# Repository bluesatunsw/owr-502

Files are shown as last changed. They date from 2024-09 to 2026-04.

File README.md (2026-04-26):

# owr
This repo includes all software necessary to operate the Test Rover Platform
that is being designed and developed in the OWR project.

## System Setup
A guide is available on the
[owr-docs](https://github.com/bluesatunsw/owr-docs/tree/main/src/guides/container_setup.md)
repository.

## Useful Command index
| Command | Effect |
| --- | --- |
| `podman compose -f "$PWD/.devcontainer/docker-compose.yml" up -d` | Run in the git root to build/restart/start the Docker container. |
| `podman compose -f "$PWD/.devcontainer/docker-compose-obc.yml" up -d` | Run in the git root to build/restart/start the Docker container **with obc specific settings!** |
| `podman exec -it --latest /bin/bash` | Enter the docker container after launching it with the devcontainer. |
| `./utils/init.bash` | Run after `cd`'ing into `/workspaces/owr` in the container to source the ROS env and tools |
| `colcon build --symlink-install` | Runs the `colcon` meta build system, builds ALL rover packages! |
| `ros2 launch rover rover.launch.py` | Launch the robot state publisher. Just leave this running. |
| `rqt` | The flexible ROS2 viewer, useful for debugging topic flows and looking at raw topics. |
| `rviz2` | Useful for visualizing TF2 / LiDAR / etc... data to see if it looks okay. |
| `podman rm --force --latest -t 0` | Kill the podman container with the latest creation date (quickly) |

NOTE: `podman compose` will take a VERY long time! on uni Wi-Fi \~5min due to
the amount of packages it installs (\~5GB). There is also [a podman
bug](github.com/containers/podman/issues/16541) that invokes a postprocessing
step on the overlay filesystem, this will take **upwards of 10 minutes!** 

NOTE: `./utils/init.bash` will source the appropriate files as well as put you
in a 10-deep nested shell - running an invalid command will kill 1 level!

### Less Common Commands

| Command | Effect |
| --- | --- |
| `ros2 launch rover rsp.launch.py` | Robot State Publisher, publishes the URDF+JSP, to make it viewable in Lichtblick / Rviz2. |
| `xacro ./src/rover/description/robot.urdf.xacro > ./build/rover.urdf` | Compiles the xacro into a singular urdf file |
| `ros2 run key_teleop key_teleop --ros-args -p twist_stamped_enabled:=True -r /key_vel:=/diff_drive_base_controller/cmd_vel` | Record keyboard imputs and publish them as Twist2d values, which ROS2Control is listening for! |

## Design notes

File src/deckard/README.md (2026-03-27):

# REPL for controlling the rover over Cyphal

Run the program:
`deckard <stepper can interface> <VESC can interface> <OBC node ID>`

e.g. `deckard can0 can1 43`

The program has integrated help.

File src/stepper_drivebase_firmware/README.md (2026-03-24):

# Stepper drivebase firmware

See also `main.rs` (and maybe `Cargo.toml`).

## Firmware organisation

This crate uses the `embedded_common` crate, which should be shipped and
checked out in this crate's parent directory (see `Cargo.toml`). This provides
STM32G4-specific drivers that are reused across Bluesat firmware for different
boards (e.g. Cyphal/canadensis FDCAN driver), and some other tools (e.g.
OpenOCD config files), which should be clear reading the following section.

Otherwise, we have a pretty normal-style flat module hierarchy.

## Running and debugging the firmware

To run the firmware in a debugging/development context with an ST-LINK connected:

```
openocd -f ../embedded_common/tools/stm32g4x.cfg
cargo run --release
```

It's pretty much necessary to run in release mode due to space optimisations
being necessary to fit onto the dozens of KB of device flash.

To flash the firmware *and have it continue to run after you disconnect the
debugger* (for integration testing, or the competition (!)), do *not* run
OpenOCD. Instead, with the debugger connected, run:

```
cargo flash --release --chip stm32g474rbtx
```

(You may need to install `cargo flash`.)

Ideally, we would add extra configuration to the different release profiles
(i.e. `debug` and `release`) so that `debug` actually fits into the flash *and*
provides a nonzero amount of helpful debug information, but we haven't gotten
around to doing this yet. (Keen beans, take note!)

## A note on DSDL

The `dsdl/` directory has been removed since we don't currently plan to use any
non-publically regulated types. If we ever do need them then just create the
directory again and add the types as in the `canadensis_mvp` crate (available
at all good Bluesat repositories near you).

## Message IDs for Cyphal

For the stepper motor, subject-IDs for drive commands are in the form `30xy`:

- `30` means the message is intended for the drivebase
- `x` is the channel identifier:
    - 0 to 3 refer to the front-left (FL), front-right (FR), back-left (BL) and
      back-right (BR) motors respectively (in the context of the drivebase).
      These also correspond to the CH0 to CH3 designations as printed on the
      board's silkscreen.
- `y` is the "topic", which currently has underspecified semantics. Just use `0`.

A message with subject-ID 3020, for example, is a drive command targeting the
back-left stepper motor.

## A historical note

This firmware formerly had provisions for being flashed to multiple different
chips across the STM32G4 and G0 families, with the target board being specified
as a build feature. This mechanism is demonstrated in `canadensis_mvp`. To
avoid stretching development effort too thinly, this has since been removed.
The current policy is that this firmware will always target and be maintained
solely for the latest revision of the board, which as of the time of writing
is:

Rev. 3p0

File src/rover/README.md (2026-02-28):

## Structure of description folder

`<xacro:include>`'s / xacro files in general are processed with a guaranteed evaluation order (top to bottom).

Thus all 'helper' files used across multiple subfiles have been included directly in the largest scope, `robot.urdf.xacro`

- robot.urdf.xacro
    - utils/inertial_macros.xacro
    - utils/materials.xacro
    - chassis/chassis.xacro
    - drivebase/drivebase.xacro
        - drivebase/db_helpers.xacro
        - ros2_control.xacro
    - utils/gazebo_plugins.xacro

## Important launch files
- `rsp.launch.py`
  - This will use the URDF to show a model of the rover and the full TF tree
  - Use rviz2 to view this, 
    - set `Fixed Frame` to `base_link`
    - Add a RobotModel, set `Description Topic` to `/robot_description`
    - (Optional) add a TF

- `simulation.launch.py`
  - This will launch a simulation of the **entire rover** (with a swerve drivebase)
  - It will launch a gazebosim window with the simulated 'moon' environment
  - You may use rviz2 to view joint states etc..

### You may also want to launch:

- `ros2 run key_teleop key_teleop --ros-args -p twist_stamped_enabled:=True -r /key_vel:=/swerve_drive_base_controller/cmd_vel`
    - Runs a small TUI application that listens to arrow keys, and publishes a twist based on this (used for driving around the robot)
    - You will need to install `ros-jazzy-key-teleop` (with apt) first

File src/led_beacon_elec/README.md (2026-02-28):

# LED Beacon

I've measured it to be around 155mm wide by 40mm tall

This is gonna cost around $29

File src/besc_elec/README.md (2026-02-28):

# NOTES FROM CREATOR

### Datasheets:
- DRV8301 Gate Driver https://www.ti.com/lit/ds/symlink/drv8301.pdf

## TODO
- Replace VESC volder with this one
- Footprints for the mosfets

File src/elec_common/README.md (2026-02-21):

# Common electrical symbol and footprint library

*a.k.a. the "Bluesat" symbol and footprint libraries*

These are KiCad 9 symbols and footprints for components used across multiple
different boards that aren't part of the KiCad standard library. These are
components that are stocked in the [electrical
inventory](https://docs.google.com/spreadsheets/d/18Fax9CmlFEk7mBak5Owge5LxEZH7rAfaMM2YBqbKku0/edit?usp=sharing).
Use these symbols and footprints if they exist to save making your own symbols
and footprints for our components.

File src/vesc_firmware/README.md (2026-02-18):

# VESC Firmware 

## Running and debugging the firmware

To run the firmware in a debugging/development context with an ST-LINK connected:

```
openocd -f ../embedded_common/tools/openocd-stm32f4.cfg
cargo run --release
```

It's pretty much necessary to run in release mode due to space optimisations
being necessary to fit onto the dozens of KB of device flash.

To flash the firmware *and have it continue to run after you disconnect the
debugger* (for integration testing, or the competition (!)), do *not* run
OpenOCD. Instead, with the debugger connected, run:

```
cargo flash --release --chip stm32f446mc
```

(You may need to install `cargo flash`.)

## Current Sense Timings

DRV8301 is config'd thru resistor for 80ns deadtime
50 dts ticks @ 168MHz --> 298ns

TIM1 is on APB2, TIM1 CLK -> 168MHz, TIM1.ARR -> 6000

TIM1.CNT      0 -----up to------>  TIM.ARR   -----down to----> 0

              <------------------  35.71μs  ------------------->
TIM1.OCxREF   ⎺⎺⎺⎺⎺⎺⎺⎺⎺⎺⎺⎺⎺⎺⎺⎺⎺⎺\____________/⎺⎺⎺⎺⎺⎺⎺⎺⎺⎺⎺⎺⎺⎺⎺⎺⎺⎺
TIM1.OCx      ⎺⎺⎺⎺⎺⎺⎺⎺⎺⎺⎺⎺⎺⎺⎺⎺⎺⎺\______________/⎺⎺⎺⎺⎺⎺⎺⎺⎺⎺⎺⎺⎺⎺⎺⎺
TIM1.OCxN     ____________________/⎺⎺⎺⎺⎺⎺⎺⎺⎺⎺\__________________
                                 <> deadtime  <> 298ns
               at least 595ns   <------------> max duty limit 
TIM1.UEV      \________________________________________________/
^^^ commutation (+current PID control) interrupt (TIM1.RCR = 1, so every cycle)

ADCCLK = APB2CLK (84MHz) / 4 == 21MHz (max 36MHz)
                          vvvvv NOT TO SCALE vvvvv
ADC Samp      ______________________⎺___________________________
                                   ^ sample time 3 clks == 143ns
                                    ^ inj group trigger latency 3 clks == 143ns
ADC Conv      _______________________/⎺⎺\_______________________
               12 clks == 571ns      <-->           (doesn't affect timing 😸)

## Duty cycle limit
We need to limit the duty cycle to ensure channel A,B always have some low time
(to allow for current sensing). Assuming 0 settling time after switch

Tcurrsense = deadtime + ADC inj trig latency + ADC samp time
= 442ns (75 TIM cnt) 
~= 100 TIM1 counts (w/ settling time) (595ns) => 98.3% max duty

Aside: rust stm32f4xx-hal uses output-compare mode 1
```
PWM mode 1 - In upcounting, channel 1 is active as long as TIMx_CNT<TIMx_CCR1
else inactive. In downcounting, channel 1 is inactive (OC1REF=0) as long as
TIMx_CNT>TIMx_CCR1 else active (OC1REF=’1’).
```

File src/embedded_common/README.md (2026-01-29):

# Embedded Common

Drivers for ARGB and CAN-FD which should be used on all devices.

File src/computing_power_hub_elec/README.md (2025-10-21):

# Computing Power Hub (CPH)

A device which provides and monitors regulated rails for communications (passive 24V POE), computing (19V), cameras (12V) and lighting (5V) devices. It complies with the common device specification 2025-04.

## Switching
Output to each rail can be switched.

## Monitoring
The output current and voltage of each rail is monitored.

## Rail Generation
The 19V, 12V and 5V rails are generated by TPS54560 buck regulators (designs documented with Excel spreadsheets from TI). Each of these rails should be able to deliver 5A. A TPS61175 regulator is used to generate the 24V 1A POE rail.

The high current 5V and 12V rails replace the regular rails in the common device specification.

## Connection
Power input for the CPH is provided via a male XT30 connector. The 19V and 12V rails are output to 2-pin JST VH headers, limited to 5A and 4A respectively. LED power is sent to four ARGB (WS2812) ports with a 3-pin JST PA header, limited to 1A each.

The board has a pair of RJ45 sockets, the Ethernet signal is passed between these ports with a POE power injected into one of the ports.

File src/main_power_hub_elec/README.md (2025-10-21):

# Main Power Hub (MPH)

A device which monitors and distributes battery power onto four subcircuits (intended to be either computing power hubs or subsystem power hubs). It complies with the common device specification 2025-04.

Power input from the battery is provided via a male XT90 connector and each of the subcircuits has a female XT60 power output connector.

## Switching
Power to each of the subcircuits can be toggled by the MCU. Triggering the estop, a normally closed contact wired to the device, removes power from all subcircuits bypassing the control of the MCU. The MCU is always powered. As implied by the connector name, each channel is able to output 60A peak and 40A continuous.

Switching on ramps slowly (soft pullup resistor + gate capacitance), switching off is instantaneous.

Power MOSFET: C2902884
https://www.lcsc.com/datasheet/C2902884.pdf

BJT on pullup: BC846s
https://diotec.com/request/datasheet/bc846s.pdf

Gate drive voltage is provided by a charge pump circuit that sums the battery voltage + the 12V rail.
The gate driver is a simple BJT pullup configuration.

Charge pump MOSFET: SSM3K333R
https://toshiba.semicon-storage.com/info/SSM3K333R_datasheet_en_20250220.pdf?did=6736&prodName=SSM3K333R

## Monitoring
The bus voltage is monitored through a voltage divider into an ADC (10k / (10k + 220k)).
The output current of each channel is monitored.
This is done with a 1m shunt resistor on each channel.
The voltage across the resistor is fed into one internal STM32 op-amp per channel.
A compensation capacitor is placed on the output of each op-amp to introduce a pole near 1kHz.
The op-amp pins should be connected internally to the ADCs using software.

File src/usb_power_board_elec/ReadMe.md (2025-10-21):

# USB Power Hub

A power hub that uses battery power to operate the kinects using both a 12v rail and a 5v rail. There will also be space space on the 5v rail to power more USB devices to plug into the USB hub in the future for more communication.

USB data hub will output usb A female to communicate with USB B devices.

## Notes for creator
Notes for making the board:
- USB B into the usb data hub FROM the computer
- USB A out of the usb data hub INTO the computer
- USB output pins should ONLY cary data from the computer / hub and should ONLY have 5v rail power coming from the battery / buck converter

## TO DO
- Should decide on what part is being used as an output port at some point

- Find proper footprints for all the USB connectors

## Mega converter link
This for the setup for the VBus to 12V and Vbus to 5V
https://webench.ti.com/appinfo/webench/scripts/SDP.cgi?ID=56A75480E1E04682

This for the 12V to 1.17V and 3.3V
https://www.lcsc.com/product-detail/C327676.html

## Ampage power consumption

3v3:
- 100ma MAX per 5gb hub
- 75ma MAX for the 20g hub
- TOTAL: 500ma

## POWER PROTECTION

- 1A per USB port max
- 1.5 per 12V Kinect port MAX

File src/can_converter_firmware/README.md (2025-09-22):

# candleLight_gsusb
The actual source code (tracked with a link to upstream project) is at: https://github.com/Avnzx/bluesat_canconverter_fw.

This implements the interface of the mainline linux gs_usb kernel module and
works out-of-the-box with linux distros packaging this module, e.g. Ubuntu.

Currently, the firmware sends back an echo frame to the host when the frame is written to the CAN peripheral, and not when the frame is actually sent successfully on the bus. This affects timestamps, one-shot mode, and other edge cases.

## Known issues

Be aware that there is a bug in the gs_usb module in linux<4.5 that can crash the kernel on device removal.

Here is a fixed version that should also work for older kernels:
  https://github.com/HubertD/socketcan_gs_usb

The Firmware also implements WCID USB descriptors and thus can be used on recent Windows versions without installing a driver.

## Building

Building requires arm-none-eabi-gcc toolchain.

```shell
sudo apt-get install gcc-arm-none-eabi

mkdir build
cd build
cmake .. -DCMAKE_TOOLCHAIN_FILE=../cmake/gcc-arm-none-eabi-8-2019-q3-update.cmake

# compile a single target , e.g.
make bluesat_canconverter_fw

# Flash board (will tell app to go into DFU mode)
make flash-bluesat_canconverter_fw

#
# to list possible targets :
make help

```

## Download Binaries
Prebuilt binaries can be downloaded by clicking . On the workflow overview page, select the latest workflow that ran on master branch. The firmware artifacts can downloaded by clicking them at the bottom of the page.

## Flashing

Flashing candleLight on linux: (source: [https://cantact.io/cantact/users-guide.html](https://cantact.io/cantact/users-guide.html))
- Flashing requires the dfu-util tool. On Ubuntu, this can be installed with `sudo apt install dfu-util`.
- compile as above, or download the current binary release: gsusb_cantact_8b2b2b4.bin
- If dfu-util fails due to permission issues on Linux, you may need additional udev rules. Consult your distro's documentation and see `70-candle-usb.rules` provided here.

### recommended simple method
- If compiling with cmake, `make flash-<targetname_fw>`, e.g. `make flash-canable_fw`, to invoke dfu-util.

### method for reflashing a specific device by serial
- when multiple devices are connected, dfu-util may be unable to choose which one to flash.
- Obtain device's serial # by looking at `dfu-util -l`
- adapt the following command accordingly :
 `dfu-util -D CORRECT_FIRMWARE.bin -S "serial_number_here", -a 0 -s 0x08000000:leave`
- note, the `:leave` suffix above may not be supported by older builds of dfu-util and is simply a convenient way to reboot into the normal firmware.

### fail-safe method (or if flashing a blank device)
- Disconnect the USB connector from the CANtact, short the BOOT pins, then reconnect the USB connector. The device should enumerate as "STM32 BOOTLOADER".

- invoke dfu-util manually with: `sudo dfu-util --dfuse-address -d 0483:df11 -c 1 -i 0 -a 0 -s 0x08000000 -D CORRECT_FIRMWARE.bin` where CORRECT_FIRMWARE is the name of the desired .bin.
- Disconnect the USB connector, un-short the BOOT pins, and reconnect.

## Associating persistent device names
With udev on linux, it is possible to assign a device name to a certain serial number (see udev manpages and [systemd.link](https://www.freedesktop.org/software/systemd/man/systemd.link.html)).
This can be useful when multiple devices are connected at the same time.

An example configuration :

```
 $ cat /etc/systemd/network/60-persistent-candev.link
[Match]
Property=ID_MODEL=cannette_gs_usb ID_SERIAL_SHORT="003800254250431420363230"

[Link]
# from systemd.link manpage:
# Note that specifying a name that the kernel might use for another interface (for example "eth0") is dangerous because the name assignment done by udev will race with the assignment done by the kernel, and only one
#   interface may use the name. Depending on the order of operations, either udev or the kernel will win, making the naming unpredictable. It is best to use some different prefix

Name=cannette99
```

( The serial number can be found with the `lsusb` utility). After reloading systemd units and resetting this board :

```
 $ ip a
....
59: cannette99: <NOARP,ECHO> mtu 16 qdisc noop state DOWN group default qlen 10
    link/can
 $
```

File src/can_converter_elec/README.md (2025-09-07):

# Can Converter

USB <-> CANFD Device, based on the upstream CandleLightFD project (STM32G4 variant)

A small USB-C device that allows for the reading of can signals from the rover.

The device uses 5V power from the USB-C port to power, with a buck converter for the 3.3V power on the board. The CAN signals are processed by the TCAN1462V transceiver. The transceiver is connected to the STM32 with data signals RXD, TXD and a standby input. The STM32 also interfaces with two LEDs to display the functionality of the device and actions it's currently performing. CAN signals are processed by the STM32 and sent to the USB-C port to be used for debugging purposes.

# Can Bus Pinout

| Pin | Signal | Colour |
| --- | --- | --- |
|  1  | `CANL` | Green  |
|  2  | `CANH` | Yellow |

# Debug Pinout

| Pin | Signal  |
| --- | --- |
|  1  | `SWDIO` |
|  2  | `SWCLK` |
|  3  | `GND` |
|  4  | `VDD` |
|  5  | `SWO` |
|  6  | `NRST`  |

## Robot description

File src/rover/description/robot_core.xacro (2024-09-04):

<?xml version="1.0"?>
<robot xmlns:xacro="http://www.ros.org/wiki/xacro" >

    <xacro:include filename="inertial_macros.xacro"/>


    <xacro:property name="chassis_length" value="0.600"/>
    <xacro:property name="chassis_width" value="0.450"/>
    <xacro:property name="chassis_height" value="0.100"/>
    <xacro:property name="chassis_mass" value="10.0"/> 

    <xacro:property name="diff_bar_bearing_seat_width" value="0.04"/>
    <xacro:property name="diff_bar_length" value="0.600"/>


    <xacro:property name="wheel_radius" value="0.033"/>
    <xacro:property name="wheel_thickness" value="0.026"/>
    <xacro:property name="wheel_mass" value="0.05"/>
    <xacro:property name="wheel_offset_x" value="0.226"/>
    <xacro:property name="wheel_offset_y" value="0.3"/>
    <xacro:property name="wheel_offset_z" value="0.01"/>

    <material name="white">
        <color rgba="1 1 1 1" />
    </material>

    <material name="orange">
        <color rgba="1 0.3 0.1 1"/>
    </material>

    <material name="blue">
        <color rgba="0.2 0.2 1 1"/>
    </material>

    <material name="black">
        <color rgba="0 0 0 1"/>
    </material>

    <material name="red">
        <color rgba="1 0 0 1"/>
    </material>

    <!-- BASE LINK -->

    <link name="base_link">
    </link>


    <!-- CHASSIS LINK -->

    <joint name="chassis_joint" type="fixed">
        <parent link="base_link"/>
        <child link="chassis"/>
        <origin xyz="0 0 0"/>
    </joint>

    <link name="chassis">
        <visual>
            <origin xyz="0 0 0"/>
            <geometry>
                <box size="${chassis_length} ${chassis_width} ${chassis_height}"/>
            </geometry>
            <material name="orange"/>
        </visual>
        <xacro:inertial_box mass="15" x="${chassis_length}" y="${chassis_width}" z="${chassis_height}">
            <origin xyz="0 0 0" rpy="0 0 0"/>
        </xacro:inertial_box>
    </link>

    <gazebo reference="chassis">
        <material>Gazebo/Orange</material>
    </gazebo>

    <!-- LEFT SIDE STUFF -->
    <!-- TODO: Fix effort and velocity limits. Current values are arbitrary. -->
    <joint name="ldb_pivot_joint" type="revolute">
        <parent link="chassis"/>
        <child link="ldb_pivot"/>
        <origin xyz="0 ${chassis_width/2 + 0.014 + diff_bar_bearing_seat_width} 0" rpy="-${pi/2} 0 0" />
        <axis xyz="0 0 1"/>
        <limit lower="${-pi/6}" upper="${pi/6}" effort="80.0" velocity="10.0"/>
    </joint>

    <link name="ldb_pivot">
        <visual>
            <geometry>
                <cylinder radius="${0.056/2}" length="${diff_bar_bearing_seat_width}"/>
            </geometry>
            <material name="blue"/>
        </visual>
    </link>


    <xacro:include filename="drivebase/db_helpers.xacro" />
    <xacro:db_module_corner prefix="db_fl" isrear="1" parent="ldb_pivot"/>
    <xacro:db_module_corner prefix="db_bl" isrear="-1" parent="ldb_pivot"/>
    
    <!-- RIGHT SIDE STUFF -->
    <!-- TODO: Fix effort and velocity limits -->
    <joint name="rdb_pivot_joint" type="continuous">
        <parent link="chassis"/>
        <child link="rdb_pivot"/>
        <origin xyz="0 -${chassis_width/2 + 0.014 + diff_bar_bearing_seat_width} 0" rpy="-${pi/2} 0 0" />
        <axis xyz="0 0 1"/>
        <limit lower="${-pi/6}" upper="${pi/6}" effort="0.0" velocity="0.0"/>
        <!-- TODO: <mimic joint="ldb_pivot_joint" multiplier="-1"/> -->
    </joint>

    <link name="rdb_pivot">
        <visual>
            <geometry>
                <cylinder radius="${0.056/2}" length="${diff_bar_bearing_seat_width}"/>
            </geometry>
            <material name="blue"/>
        </visual>
    </link>

    <xacro:db_module_corner prefix="db_fr" isrear="1" flip_x="-1" parent="rdb_pivot"/>
    <xacro:db_module_corner prefix="db_br" isrear="-1" flip_x="-1" parent="rdb_pivot"/>

</robot>

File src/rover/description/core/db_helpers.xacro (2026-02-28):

<?xml version="1.0"?>
<robot xmlns:xacro="http://www.ros.org/wiki/xacro" >
    <!-- flipped = -1, normal = 1 for flip_x and isrear -->
	<xacro:macro name="db_module_corner" params="prefix parent flip_x:=1 isrear:=1">
	<!-- This is the pivot point -->
        <joint name="${prefix}_joint" type="fixed">
            <parent link="${parent}"/>
            <child link="${prefix}"/>
            <origin xyz="${isrear*(diff_bar_length/2 + 0.056/2)} 0 0" rpy="0 0 0" />
        </joint>

        <!-- This is the "arms" connected to the steering joint -->
        <joint name="${prefix}_bar_smount_joint" type="fixed">
            <parent link="${prefix}"/>
            <child link="${prefix}_smount"/>
            <origin xyz="${isrear*0.865/8} ${0.04} ${(0.04)*flip_x}" rpy="${pi/2} 0 0" />
        </joint>

        <!-- This is the steering joint -->
        <joint name="${prefix}_smount_fork_joint" type="revolute">
            <parent link="${prefix}_smount"/>
            <child link="${prefix}_wheel_fork"/>
	        <origin xyz="${0} ${0} ${-0.213/2 - 0.03/2}" rpy="0 0 0"/>
            <axis xyz="0 0 1"/>
            <limit lower="${-pi/2}" upper="${pi/2}" effort="400" velocity="5"/>
        </joint>

        <!-- This is the actual wheel -->
        <joint name="${prefix}_fork_tyre_joint" type="continuous">
            <parent link="${prefix}_wheel_fork"/>
            <child link="${prefix}_tyre"/>
            <origin xyz="0 0 ${-0.05}" rpy="${-pi/2} 0 0" />
            <axis xyz="0 0 1"/>
            <limit effort="400" velocity="0.2"/>
        </joint>


        <!-- ALL LINKS BELOW THIS LINE -->
	<!-- arm -->
        <link name="${prefix}">
            <visual>
                <geometry>
			<box size="${0.865/2} ${diff_bar_bearing_seat_width} ${diff_bar_bearing_seat_width}"/>
		</geometry>
		<origin xyz="${isrear*-0.865/1.5} 0 0" rpy="0 0 0"/>
                <material name="orange"/>
            </visual>
	    <xacro:inertial_box mass="2" x="${0.865/2}" y="${diff_bar_bearing_seat_width}" z="${diff_bar_bearing_seat_width}">
		    <origin xyz="${isrear*-0.865/1.5} 0 0" rpy="0 0 0"/>
            </xacro:inertial_box>
        </link>

        <!-- Steering motor mount -->
        <link name="${prefix}_smount">
            <visual>
                <geometry>
                    <cylinder radius="${0.0425}" length="0.03"/>
                </geometry>
                <material name="orange"/>
            </visual>
        </link>

        <!-- The actual steering joint -->
        <link name="${prefix}_wheel_fork">
            <visual>
                <geometry>
                    <box size="0.066 0.170 0.213"/>
                </geometry>
                <material name="blue"/>                
            </visual>
            <xacro:inertial_box mass="1" x="0.066" y="0.170" z="0.213">
                <origin xyz="0 0 0" rpy="0 0 0"/>
            </xacro:inertial_box>
        </link>

        <!-- Wheel -->
        <link name="${prefix}_tyre">
            <visual>
                <geometry>
			<cylinder radius="${wheel_radius}" length="${wheel_thickness}"/>
                </geometry>
                <material name="black"/>
            </visual>
            <collision>
                <geometry>
                    <sphere radius="${wheel_radius}"/>
                </geometry>
            </collision>
            <xacro:inertial_sphere mass="2.5" radius="${0.125}" >
                <origin xyz="0 0 0" rpy="0 0 0"/>
            </xacro:inertial_sphere>
        </link>
    </xacro:macro>
</robot>

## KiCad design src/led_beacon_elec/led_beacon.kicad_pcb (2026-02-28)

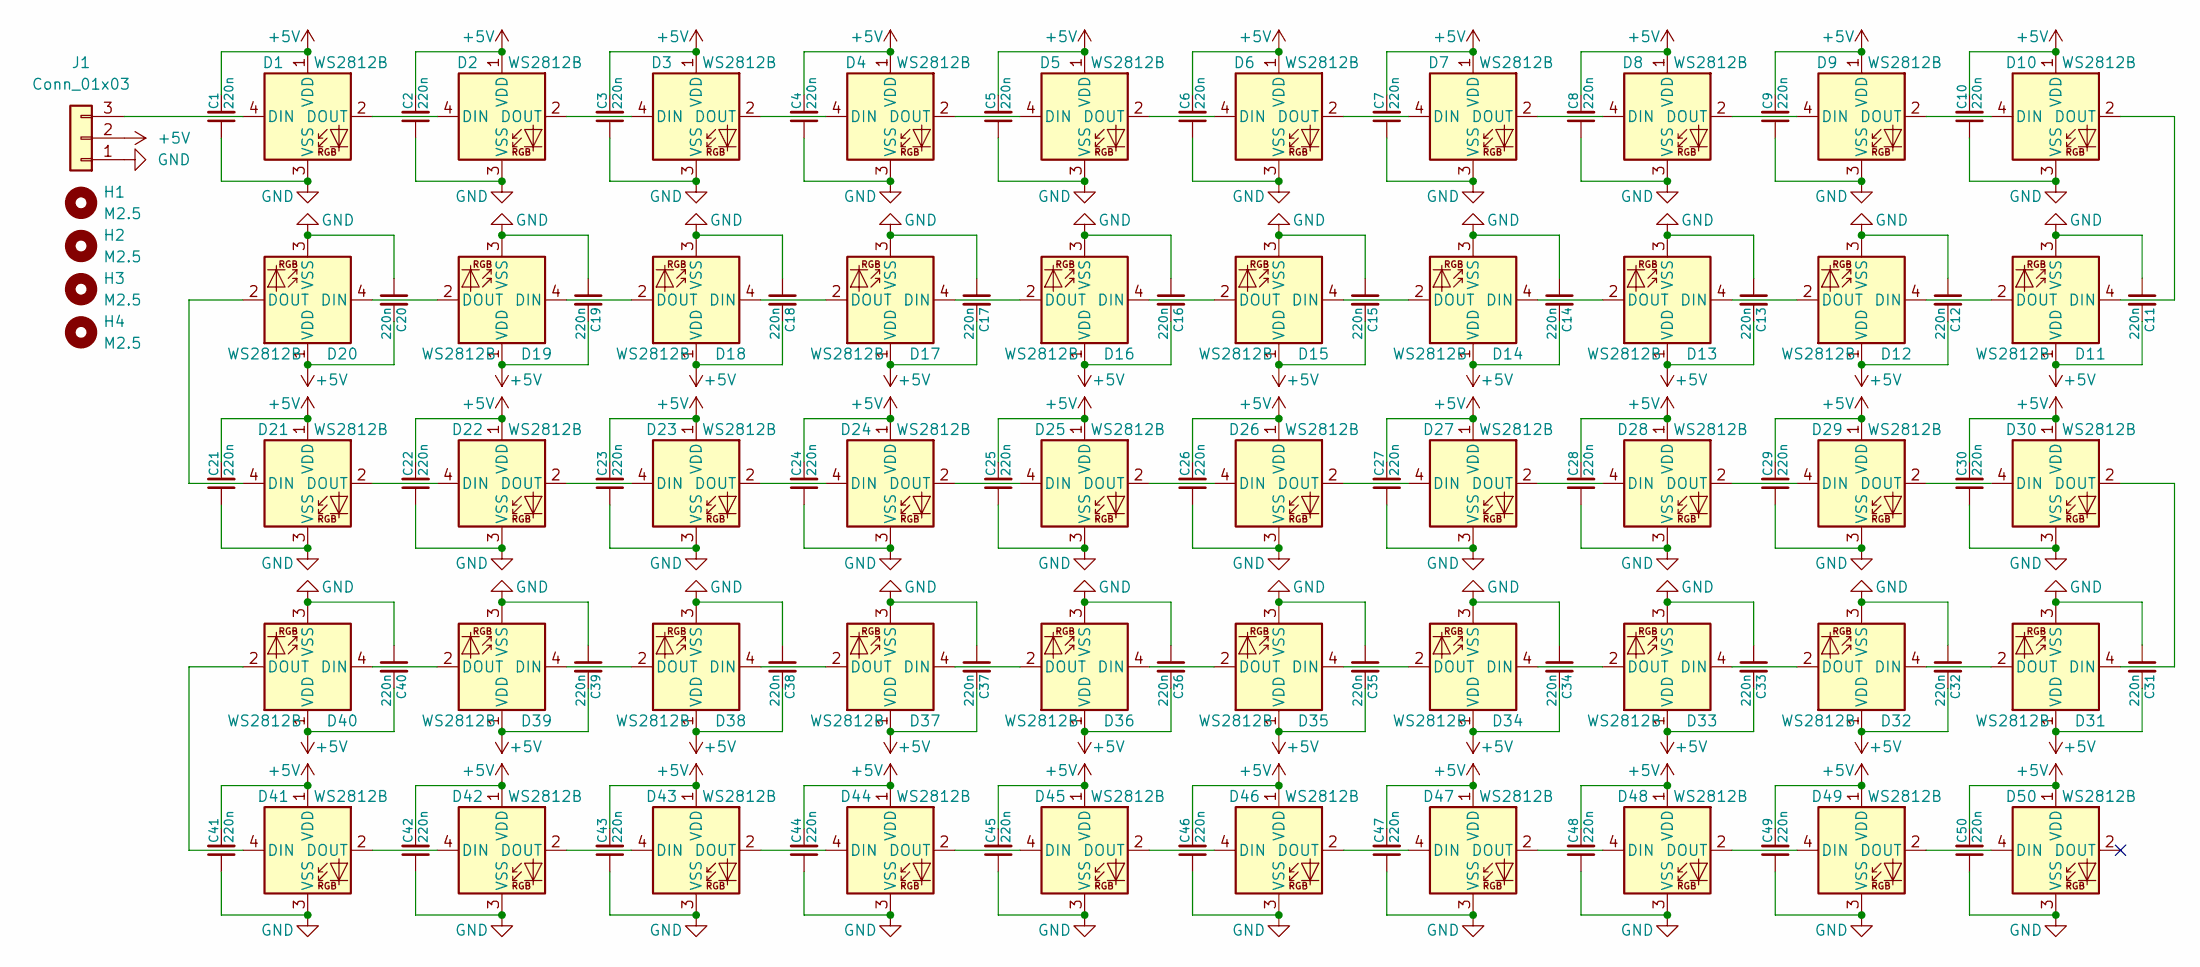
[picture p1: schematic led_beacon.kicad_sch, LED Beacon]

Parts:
C1, C2, C3, C4, C5, C6, C7, C8, C9, C10, C11, C12, C13, C14, C15, C16, C17, C18, C19, C20, C21, C22, C23, C24, C25, C26, C27, C28, C29, C30, C31, C32, C33, C34, C35, C36, C37, C38, C39, C40, C41, C42, C43, C44, C45, C46, C47, C48, C49, C50: 220n; C_0402_1005Metric; Rating 10V
D1, D2, D3, D4, D5, D6, D7, D8, D9, D10, D11, D12, D13, D14, D15, D16, D17, D18, D19, D20, D21, D22, D23, D24, D25, D26, D27, D28, D29, D30, D31, D32, D33, D34, D35, D36, D37, D38, D39, D40, D41, D42, D43, D44, D45, D46, D47, D48, D49, D50: WS2812B; WS2812B-5050
H1, H2, H3, H4: M2.5; M2.5_Internal
J1: Conn_01x03; SM03B-PASS

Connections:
+5V: C1.2, C2.2, C3.2, C4.2, C5.2, C6.2, C7.2, C8.2, C9.2, C10.2, C11.2, C12.2, C13.2, C14.2, C15.2, C16.2, C17.2, C18.2, C19.2, C20.2, C21.2, C22.2, C23.2, C24.2, C25.2, C26.2, C27.2, C28.2, C29.2, C30.2, C31.2, C32.2, C33.2, C34.2, C35.2, C36.2, C37.2, C38.2, C39.2, C40.2, C41.2, C42.2, C43.2, C44.2, C45.2, C46.2, C47.2, C48.2, C49.2, C50.2, D1.1 (VDD), D2.1 (VDD), D3.1 (VDD), D4.1 (VDD), D5.1 (VDD), D6.1 (VDD), D7.1 (VDD), D8.1 (VDD), D9.1 (VDD), D10.1 (VDD), D11.1 (VDD), D12.1 (VDD), D13.1 (VDD), D14.1 (VDD), D15.1 (VDD), D16.1 (VDD), D17.1 (VDD), D18.1 (VDD), D19.1 (VDD), D20.1 (VDD), D21.1 (VDD), D22.1 (VDD), D23.1 (VDD), D24.1 (VDD), D25.1 (VDD), D26.1 (VDD), D27.1 (VDD), D28.1 (VDD), D29.1 (VDD), D30.1 (VDD), D31.1 (VDD), D32.1 (VDD), D33.1 (VDD), D34.1 (VDD), D35.1 (VDD), D36.1 (VDD), D37.1 (VDD), D38.1 (VDD), D39.1 (VDD), D40.1 (VDD), D41.1 (VDD), D42.1 (VDD), D43.1 (VDD), D44.1 (VDD), D45.1 (VDD), D46.1 (VDD), D47.1 (VDD), D48.1 (VDD), D49.1 (VDD), D50.1 (VDD), J1.2
GND: C1.1, C2.1, C3.1, C4.1, C5.1, C6.1, C7.1, C8.1, C9.1, C10.1, C11.1, C12.1, C13.1, C14.1, C15.1, C16.1, C17.1, C18.1, C19.1, C20.1, C21.1, C22.1, C23.1, C24.1, C25.1, C26.1, C27.1, C28.1, C29.1, C30.1, C31.1, C32.1, C33.1, C34.1, C35.1, C36.1, C37.1, C38.1, C39.1, C40.1, C41.1, C42.1, C43.1, C44.1, C45.1, C46.1, C47.1, C48.1, C49.1, C50.1, D1.3 (VSS), D2.3 (VSS), D3.3 (VSS), D4.3 (VSS), D5.3 (VSS), D6.3 (VSS), D7.3 (VSS), D8.3 (VSS), D9.3 (VSS), D10.3 (VSS), D11.3 (VSS), D12.3 (VSS), D13.3 (VSS), D14.3 (VSS), D15.3 (VSS), D16.3 (VSS), D17.3 (VSS), D18.3 (VSS), D19.3 (VSS), D20.3 (VSS), D21.3 (VSS), D22.3 (VSS), D23.3 (VSS), D24.3 (VSS), D25.3 (VSS), D26.3 (VSS), D27.3 (VSS), D28.3 (VSS), D29.3 (VSS), D30.3 (VSS), D31.3 (VSS), D32.3 (VSS), D33.3 (VSS), D34.3 (VSS), D35.3 (VSS), D36.3 (VSS), D37.3 (VSS), D38.3 (VSS), D39.3 (VSS), D40.3 (VSS), D41.3 (VSS), D42.3 (VSS), D43.3 (VSS), D44.3 (VSS), D45.3 (VSS), D46.3 (VSS), D47.3 (VSS), D48.3 (VSS), D49.3 (VSS), D50.3 (VSS), J1.1
unnamed: D1.4 (DIN), J1.3
unnamed: D1.2 (DOUT), D2.4 (DIN)
unnamed: D2.2 (DOUT), D3.4 (DIN)
unnamed: D3.2 (DOUT), D4.4 (DIN)
unnamed: D4.2 (DOUT), D5.4 (DIN)
unnamed: D5.2 (DOUT), D6.4 (DIN)
unnamed: D6.2 (DOUT), D7.4 (DIN)
unnamed: D7.2 (DOUT), D8.4 (DIN)
unnamed: D8.2 (DOUT), D9.4 (DIN)
unnamed: D9.2 (DOUT), D10.4 (DIN)
unnamed: D10.2 (DOUT), D11.4 (DIN)
unnamed: D11.2 (DOUT), D12.4 (DIN)
unnamed: D12.2 (DOUT), D13.4 (DIN)
unnamed: D13.2 (DOUT), D14.4 (DIN)
unnamed: D14.2 (DOUT), D15.4 (DIN)
unnamed: D15.2 (DOUT), D16.4 (DIN)
unnamed: D16.2 (DOUT), D17.4 (DIN)
unnamed: D17.2 (DOUT), D18.4 (DIN)
unnamed: D18.2 (DOUT), D19.4 (DIN)
unnamed: D19.2 (DOUT), D20.4 (DIN)
unnamed: D20.2 (DOUT), D21.4 (DIN)
unnamed: D21.2 (DOUT), D22.4 (DIN)
unnamed: D22.2 (DOUT), D23.4 (DIN)
unnamed: D23.2 (DOUT), D24.4 (DIN)
unnamed: D24.2 (DOUT), D25.4 (DIN)
unnamed: D25.2 (DOUT), D26.4 (DIN)
unnamed: D26.2 (DOUT), D27.4 (DIN)
unnamed: D27.2 (DOUT), D28.4 (DIN)
unnamed: D28.2 (DOUT), D29.4 (DIN)
unnamed: D29.2 (DOUT), D30.4 (DIN)
unnamed: D30.2 (DOUT), D31.4 (DIN)
unnamed: D31.2 (DOUT), D32.4 (DIN)
unnamed: D32.2 (DOUT), D33.4 (DIN)
unnamed: D33.2 (DOUT), D34.4 (DIN)
unnamed: D34.2 (DOUT), D35.4 (DIN)
unnamed: D35.2 (DOUT), D36.4 (DIN)
unnamed: D36.2 (DOUT), D37.4 (DIN)
unnamed: D37.2 (DOUT), D38.4 (DIN)
unnamed: D38.2 (DOUT), D39.4 (DIN)
unnamed: D39.2 (DOUT), D40.4 (DIN)
unnamed: D40.2 (DOUT), D41.4 (DIN)
unnamed: D41.2 (DOUT), D42.4 (DIN)
unnamed: D42.2 (DOUT), D43.4 (DIN)
unnamed: D43.2 (DOUT), D44.4 (DIN)
unnamed: D44.2 (DOUT), D45.4 (DIN)
unnamed: D45.2 (DOUT), D46.4 (DIN)
unnamed: D46.2 (DOUT), D47.4 (DIN)
unnamed: D47.2 (DOUT), D48.4 (DIN)
unnamed: D48.2 (DOUT), D49.4 (DIN)
unnamed: D49.2 (DOUT), D50.4 (DIN)

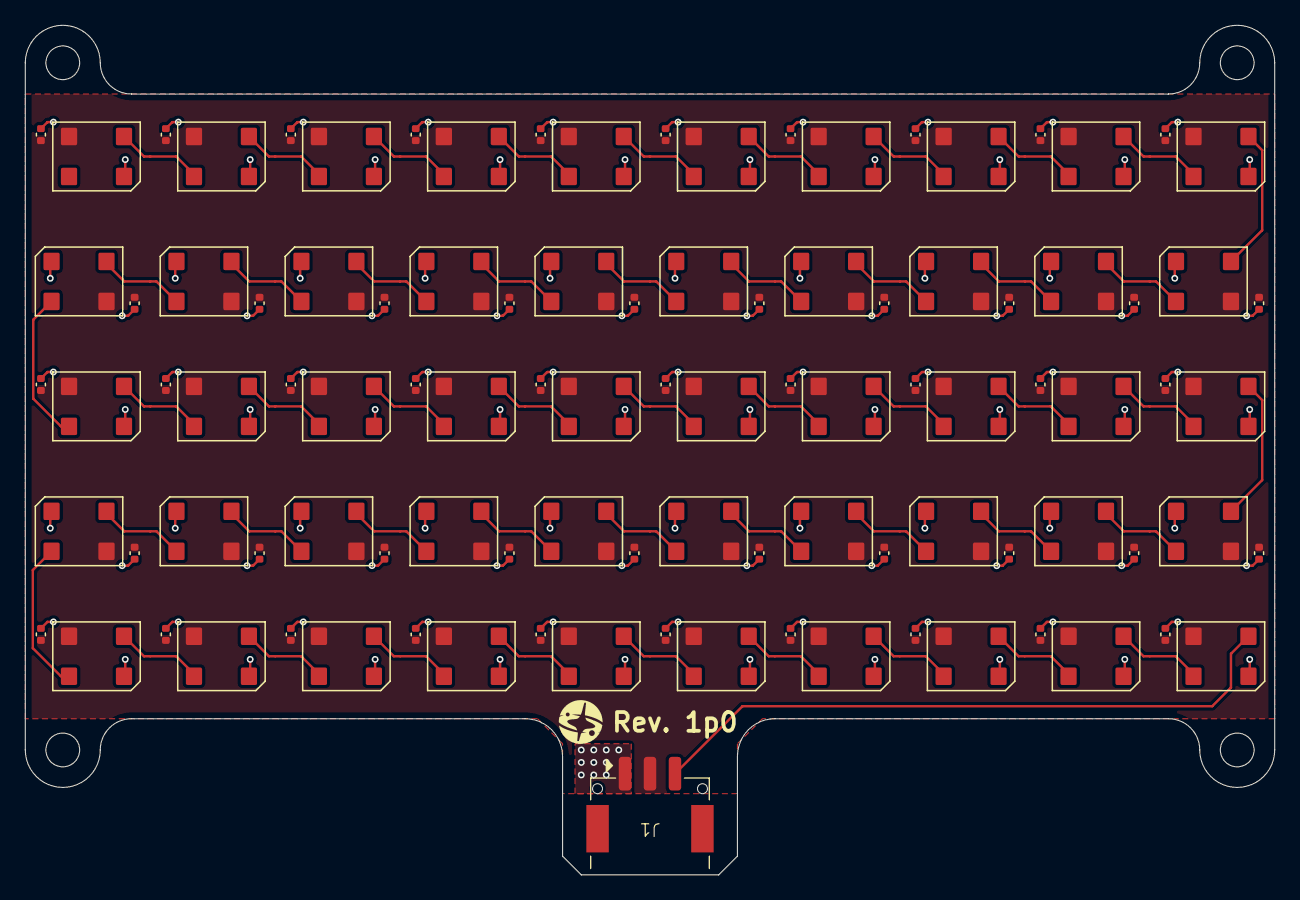
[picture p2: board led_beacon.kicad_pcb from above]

Board: 2 copper layers, 100.0 x 68.0 mm, 105 parts (0 on the bottom side), 52 nets.

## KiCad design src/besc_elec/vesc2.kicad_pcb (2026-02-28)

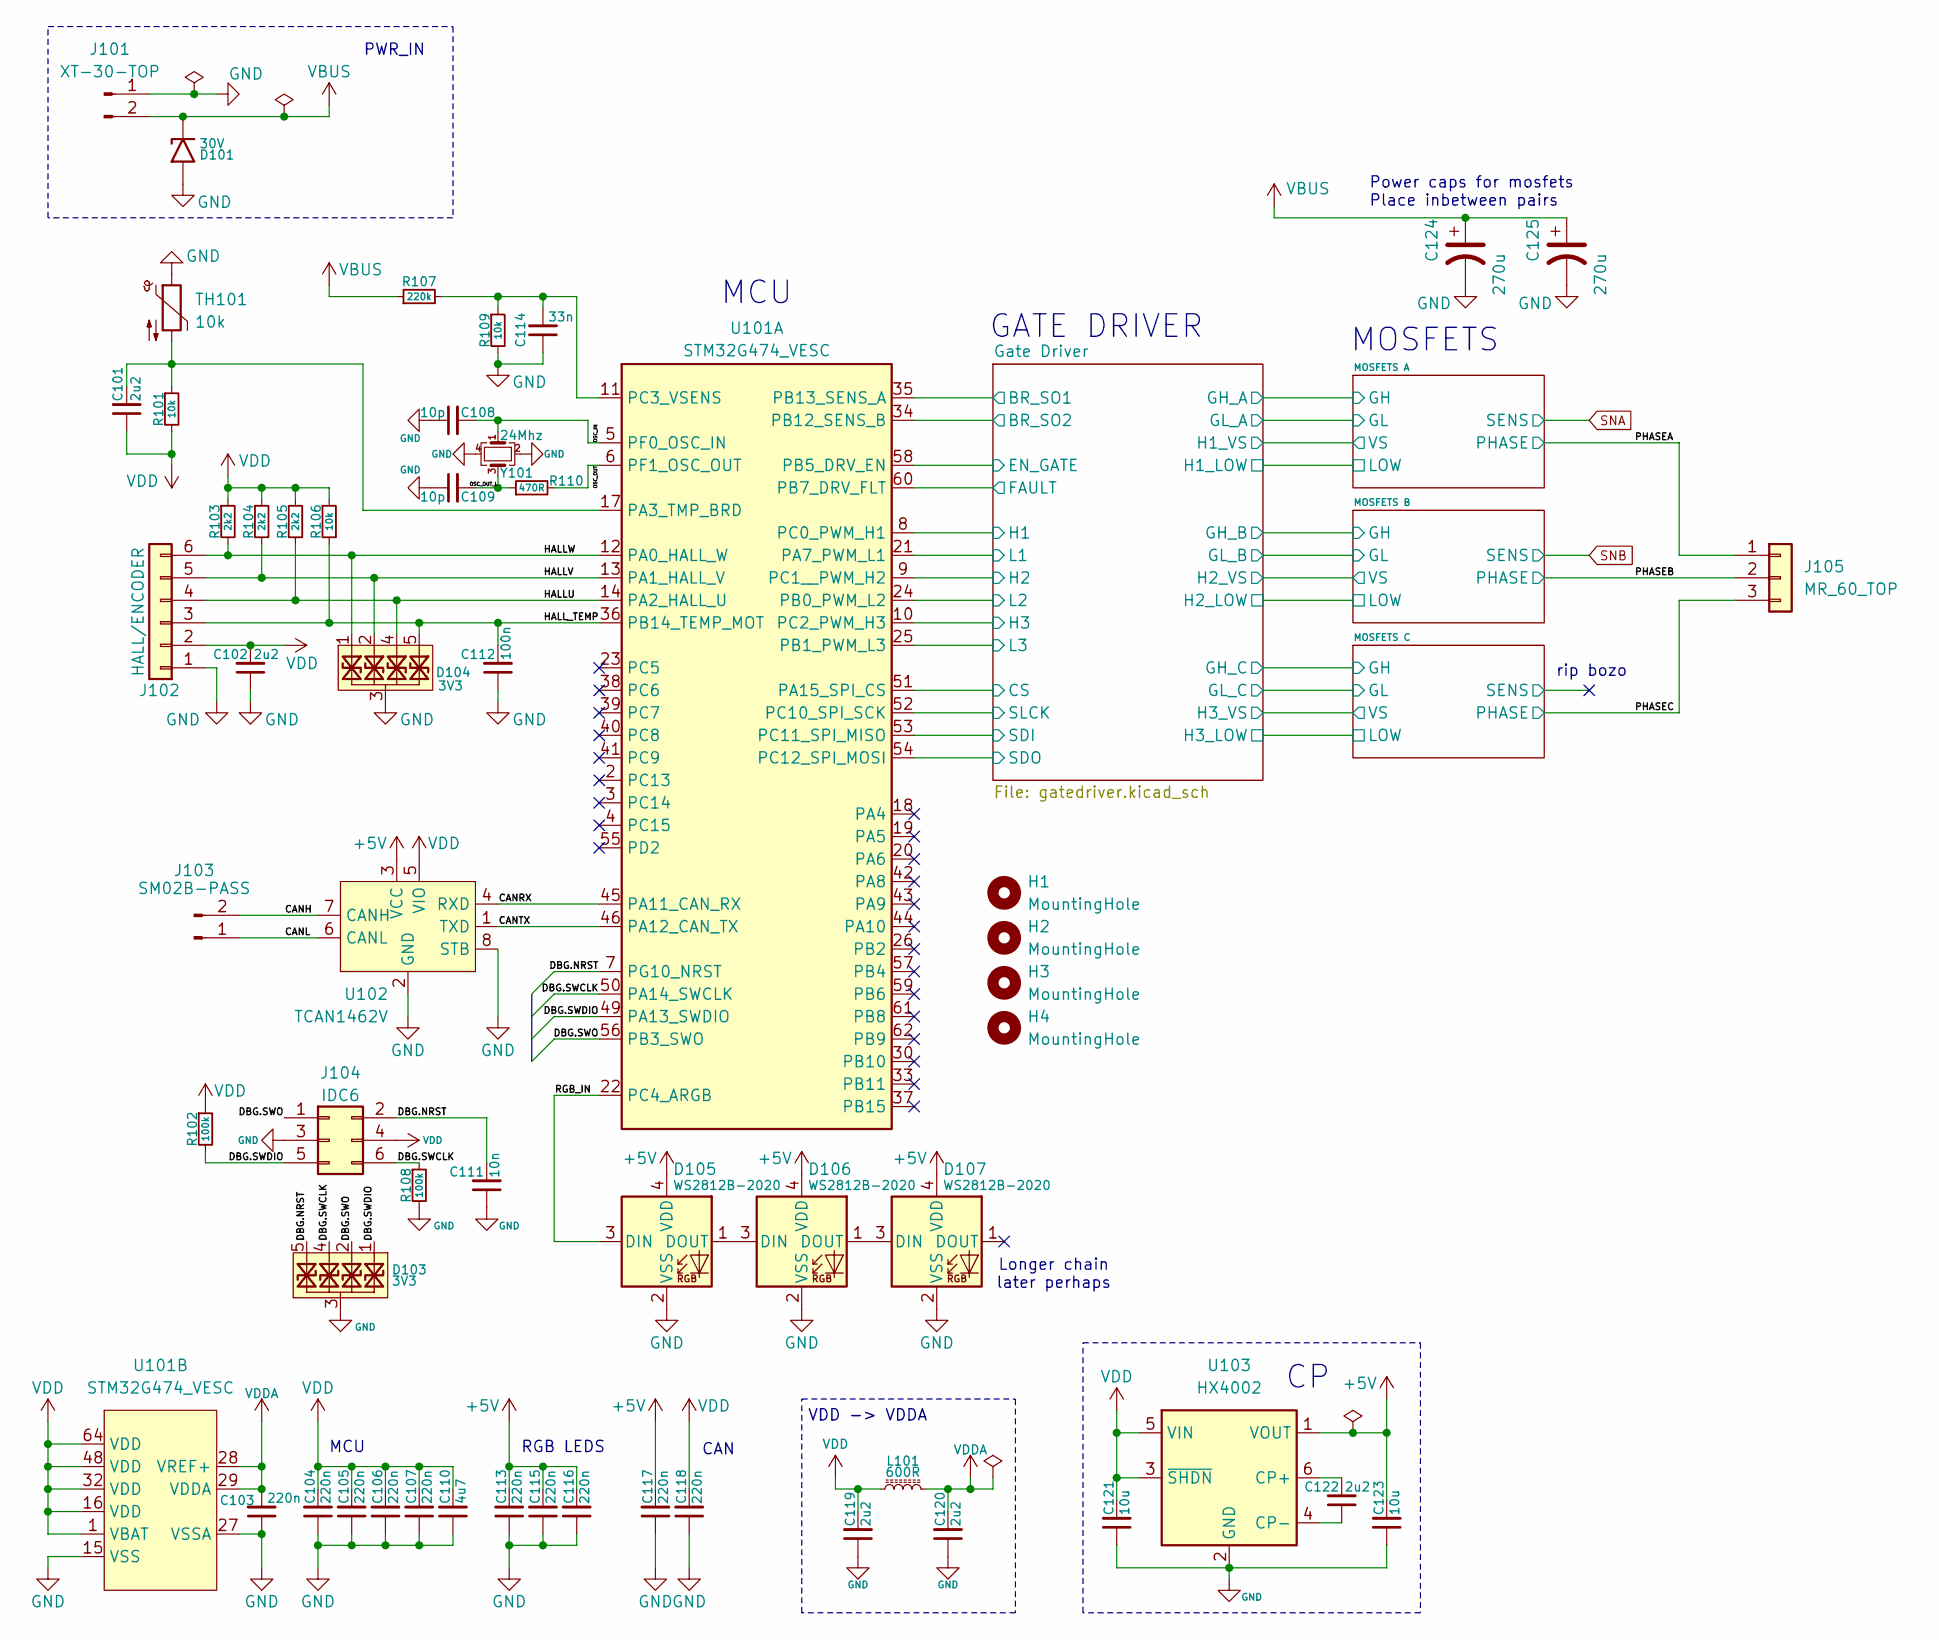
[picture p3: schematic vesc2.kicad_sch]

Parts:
C101, C102, C119, C120, C122: 2u2; C_0603_1608Metric
C103, C104, C105, C106, C107, C113, C115, C116, C117, C118: 220n; C_0402_1005Metric
C108, C109: 10p; C_0402_1005Metric
C110: 4u7; C_0805_2012Metric
C111: 10n; C_0402_1005Metric
C112: 100n; C_0402_1005Metric
C114: 33n; C_0402_1005Metric
C121, C123: 10u; C_1206_3216Metric
C124, C125: 270u; CP_Elec_10x10
D101: 30V; D_SMF
D103, D104: 3V3; Diodes_UDFN-10_1x2.5mm_P0.5mm
D105, D106, D107: WS2812B-2020
H1, H2, H3, H4: MountingHole; M2.5_Edge
J101: XT-30-TOP; XT30PW-M_1x02_P2.50mm_Top_mount
J102: HALL/ENCODER; BM06B-PASS
J103: SM02B-PASS; BM02B-PASS
J104: IDC6
J105: MR_60_TOP; MR60-F-TopMount
L101: 600R; R_0402_1005Metric
R101, R106, R109: 10k; R_0402_1005Metric
R102, R108: 100k; R_0402_1005Metric
R103, R104, R105: 2k2; R_0402_1005Metric
R107: 220k; R_0402_1005Metric
R110: 470R; R_0402_1005Metric
TH101: 10k; R_0402_1005Metric
U101: STM32G474_VESC; LQFP-64-0.5
U102: TCAN1462V; SOIC-8_3.9x4.9mm_P1.27mm
U103: HX4002; SOT-23-6
Y101: 24Mhz; Crystal_SMD_2016-4Pin_2.0x1.6mm

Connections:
+5V: C113.2, C115.2, C116.2, C117.2, C123.2, D105.4 (VDD), D106.4 (VDD), D107.4 (VDD), U102.3 (VCC), U103.1 (VOUT)
/CANH: J103.2, U102.7 (CANH)
/CANL: J103.1, U102.6 (CANL)
/CANRX: U101.45 (PA11_CAN_RX), U102.4 (RXD)
/CANTX: U101.46 (PA12_CAN_TX), U102.1 (TXD)
/DBG.NRST: C111.2, D103.5, D103.6, J104.2, U101.7 (PG10_NRST)
/DBG.SWCLK: D103.4, D103.7, J104.6, R108.1, U101.50 (PA14_SWCLK)
/DBG.SWDIO: D103.1, D103.10, J104.5, R102.2, U101.49 (PA13_SWDIO)
/DBG.SWO: D103.2, D103.9, J104.1, U101.56 (PB3_SWO)
/Gate Driver/BR_SO1: U101.35 (PB13_SENS_A); also elsewhere on the board
/Gate Driver/BR_SO2: U101.34 (PB12_SENS_B); also elsewhere on the board
/Gate Driver/CS: U101.51 (PA15_SPI_CS); also elsewhere on the board
/Gate Driver/EN_GATE: U101.58 (PB5_DRV_EN); also elsewhere on the board
/Gate Driver/FAULT: U101.60 (PB7_DRV_FLT); also elsewhere on the board
/Gate Driver/H1: U101.8 (PC0_PWM_H1); also elsewhere on the board
/Gate Driver/H2: U101.9 (PC1__PWM_H2); also elsewhere on the board
/Gate Driver/H3: U101.10 (PC2_PWM_H3); also elsewhere on the board
/Gate Driver/L1: U101.21 (PA7_PWM_L1); also elsewhere on the board
/Gate Driver/L2: U101.24 (PB0_PWM_L2); also elsewhere on the board
/Gate Driver/L3: U101.25 (PB1_PWM_L3); also elsewhere on the board
/Gate Driver/SDI: U101.53 (PC11_SPI_MISO); also elsewhere on the board
/Gate Driver/SDO: U101.54 (PC12_SPI_MOSI); also elsewhere on the board
/Gate Driver/SLCK: U101.52 (PC10_SPI_SCK); also elsewhere on the board
/HALLU: D104.4, D104.7, J102.4, R105.2, U101.14 (PA2_HALL_U)
/HALLV: D104.2, D104.9, J102.5, R104.2, U101.13 (PA1_HALL_V)
/HALLW: D104.1, D104.10, J102.6, R103.2, U101.12 (PA0_HALL_W)
/HALL_TEMP: C112.2, D104.5, D104.6, J102.3, R106.2, U101.36 (PB14_TEMP_MOT)
/OSC_IN: C108.2, U101.5 (PF0_OSC_IN), Y101.1
/OSC_OUT: R110.2, U101.6 (PF1_OSC_OUT)
/OSC_OUT_L: C109.2, R110.1, Y101.3
/PHASEA: J105.1; also elsewhere on the board
/PHASEB: J105.2; also elsewhere on the board
/PHASEC: J105.3; also elsewhere on the board
/RGB_IN: D105.3 (DIN), U101.22 (PC4_ARGB)
GND: C102.1, C103.1, C104.1, C105.1, C106.1, C107.1, C108.1, C109.1, C110.1, C111.1, C112.1, C113.1, C114.1, C115.1, C116.1, C117.1, C118.1, C119.1, C120.1, C121.1, C123.1, C124.2, C125.2, D101.2 (A2), D103.3, D103.8, D104.3, D104.8, D105.2 (VSS), D106.2 (VSS), D107.2 (VSS), J101.1, J102.1, J104.3, R108.2, R109.2, TH101.1, U101.15 (VSS), U101.27 (VSSA), U101.31 (VSS), U101.47 (VSS), U101.63 (VSS), U102.2 (GND), U102.8 (STB), U102.9 (EP), U103.2 (GND), Y101.2, Y101.4; also elsewhere on the board
unnamed: D105.1 (DOUT), D106.3 (DIN)
unnamed: D106.1 (DOUT), D107.3 (DIN)
unnamed: C101.2, R101.1, TH101.2, U101.17 (PA3_TMP_BRD)
unnamed: C114.2, R107.2, R109.1, U101.11 (PC3_VSENS)
unnamed: C122.2, U103.6 (CP+)
unnamed: C122.1, U103.4 (CP-)
VBUS: C124.1, C125.1, D101.1 (A1), J101.2, R107.1; also elsewhere on the board
VDD: C101.1, C102.2, C104.2, C105.2, C106.2, C107.2, C110.2, C118.2, C119.2, C121.2, J102.2, J104.4, L101.1, R101.2, R102.1, R103.1, R104.1, R105.1, R106.1, U101.1 (VBAT), U101.16 (VDD), U101.32 (VDD), U101.48 (VDD), U101.64 (VDD), U102.5 (VIO), U103.3 (~SHDN), U103.5 (VIN); also elsewhere on the board
VDDA: C103.2, C120.2, L101.2, U101.28 (VREF+), U101.29 (VDDA)

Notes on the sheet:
RGB LEDS
Power caps for mosfets Place inbetween pairs
rip bozo
GATE DRIVER
MCU
CAN
VDD -> VDDA
MOSFETS
Longer chain later perhaps
PWR_IN

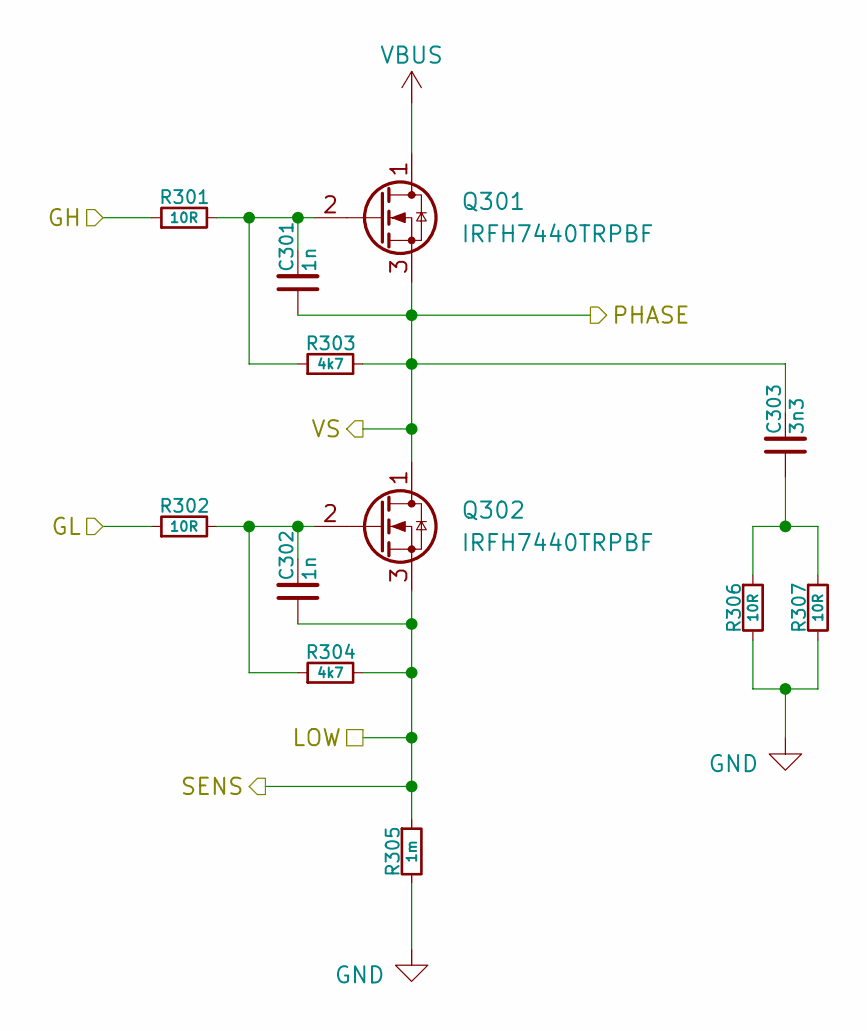
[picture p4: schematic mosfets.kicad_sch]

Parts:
C301, C302: 1n; C_0402_1005Metric
C303: 3n3; C_0402_1005Metric
Q301, Q302: IRFH7440TRPBF; PQFN_5x6mm_E_DGS
R301, R302, R306, R307: 10R; R_0402_1005Metric
R303, R304: 4k7; R_0402_1005Metric
R305: 1m; R_2512_6332Metric

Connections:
/Gate Driver/GH_A: R301.1; also elsewhere on the board
/Gate Driver/GL_A: R302.1; also elsewhere on the board
/PHASEA: C301.1, C303.2, Q301.3 (S), Q302.1 (D), R303.2; also elsewhere on the board
GND: R305.2, R306.2, R307.2; also elsewhere on the board
unnamed: C303.1, R306.1, R307.1
unnamed: C301.2, Q301.2 (G), R301.2, R303.1
unnamed: C302.2, Q302.2 (G), R302.2, R304.1
SNA: C302.1, Q302.3 (S), R304.2, R305.1; also elsewhere on the board
VBUS: Q301.1 (D); also elsewhere on the board

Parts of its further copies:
C401, C402, C501, C502: 1n; C_0402_1005Metric
C403, C503: 3n3; C_0402_1005Metric
Q401, Q402, Q501, Q502: IRFH7440TRPBF; PQFN_5x6mm_E_DGS
R401, R402, R406, R407, R501, R502, R506, R507: 10R; R_0402_1005Metric
R403, R404, R503, R504: 4k7; R_0402_1005Metric
R405, R505: 1m; R_2512_6332Metric

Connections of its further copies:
/Gate Driver/GH_B: R401.1; also elsewhere on the board
/Gate Driver/GH_C: R501.1; also elsewhere on the board
/Gate Driver/GL_B: R402.1; also elsewhere on the board
/Gate Driver/GL_C: R502.1; also elsewhere on the board
/Gate Driver/H3_LOW: C502.1, Q502.3 (S), R504.2, R505.1; also elsewhere on the board
/PHASEB: C401.1, C403.2, Q401.3 (S), Q402.1 (D), R403.2; also elsewhere on the board
/PHASEC: C501.1, C503.2, Q501.3 (S), Q502.1 (D), R503.2; also elsewhere on the board
GND: R405.2, R406.2, R407.2, R505.2, R506.2, R507.2; also elsewhere on the board
unnamed: C403.1, R406.1, R407.1
unnamed: C503.1, R506.1, R507.1
unnamed: C401.2, Q401.2 (G), R401.2, R403.1
unnamed: C402.2, Q402.2 (G), R402.2, R404.1
unnamed: C501.2, Q501.2 (G), R501.2, R503.1
unnamed: C502.2, Q502.2 (G), R502.2, R504.1
SNB: C402.1, Q402.3 (S), R404.2, R405.1; also elsewhere on the board
VBUS: Q401.1 (D), Q501.1 (D); also elsewhere on the board

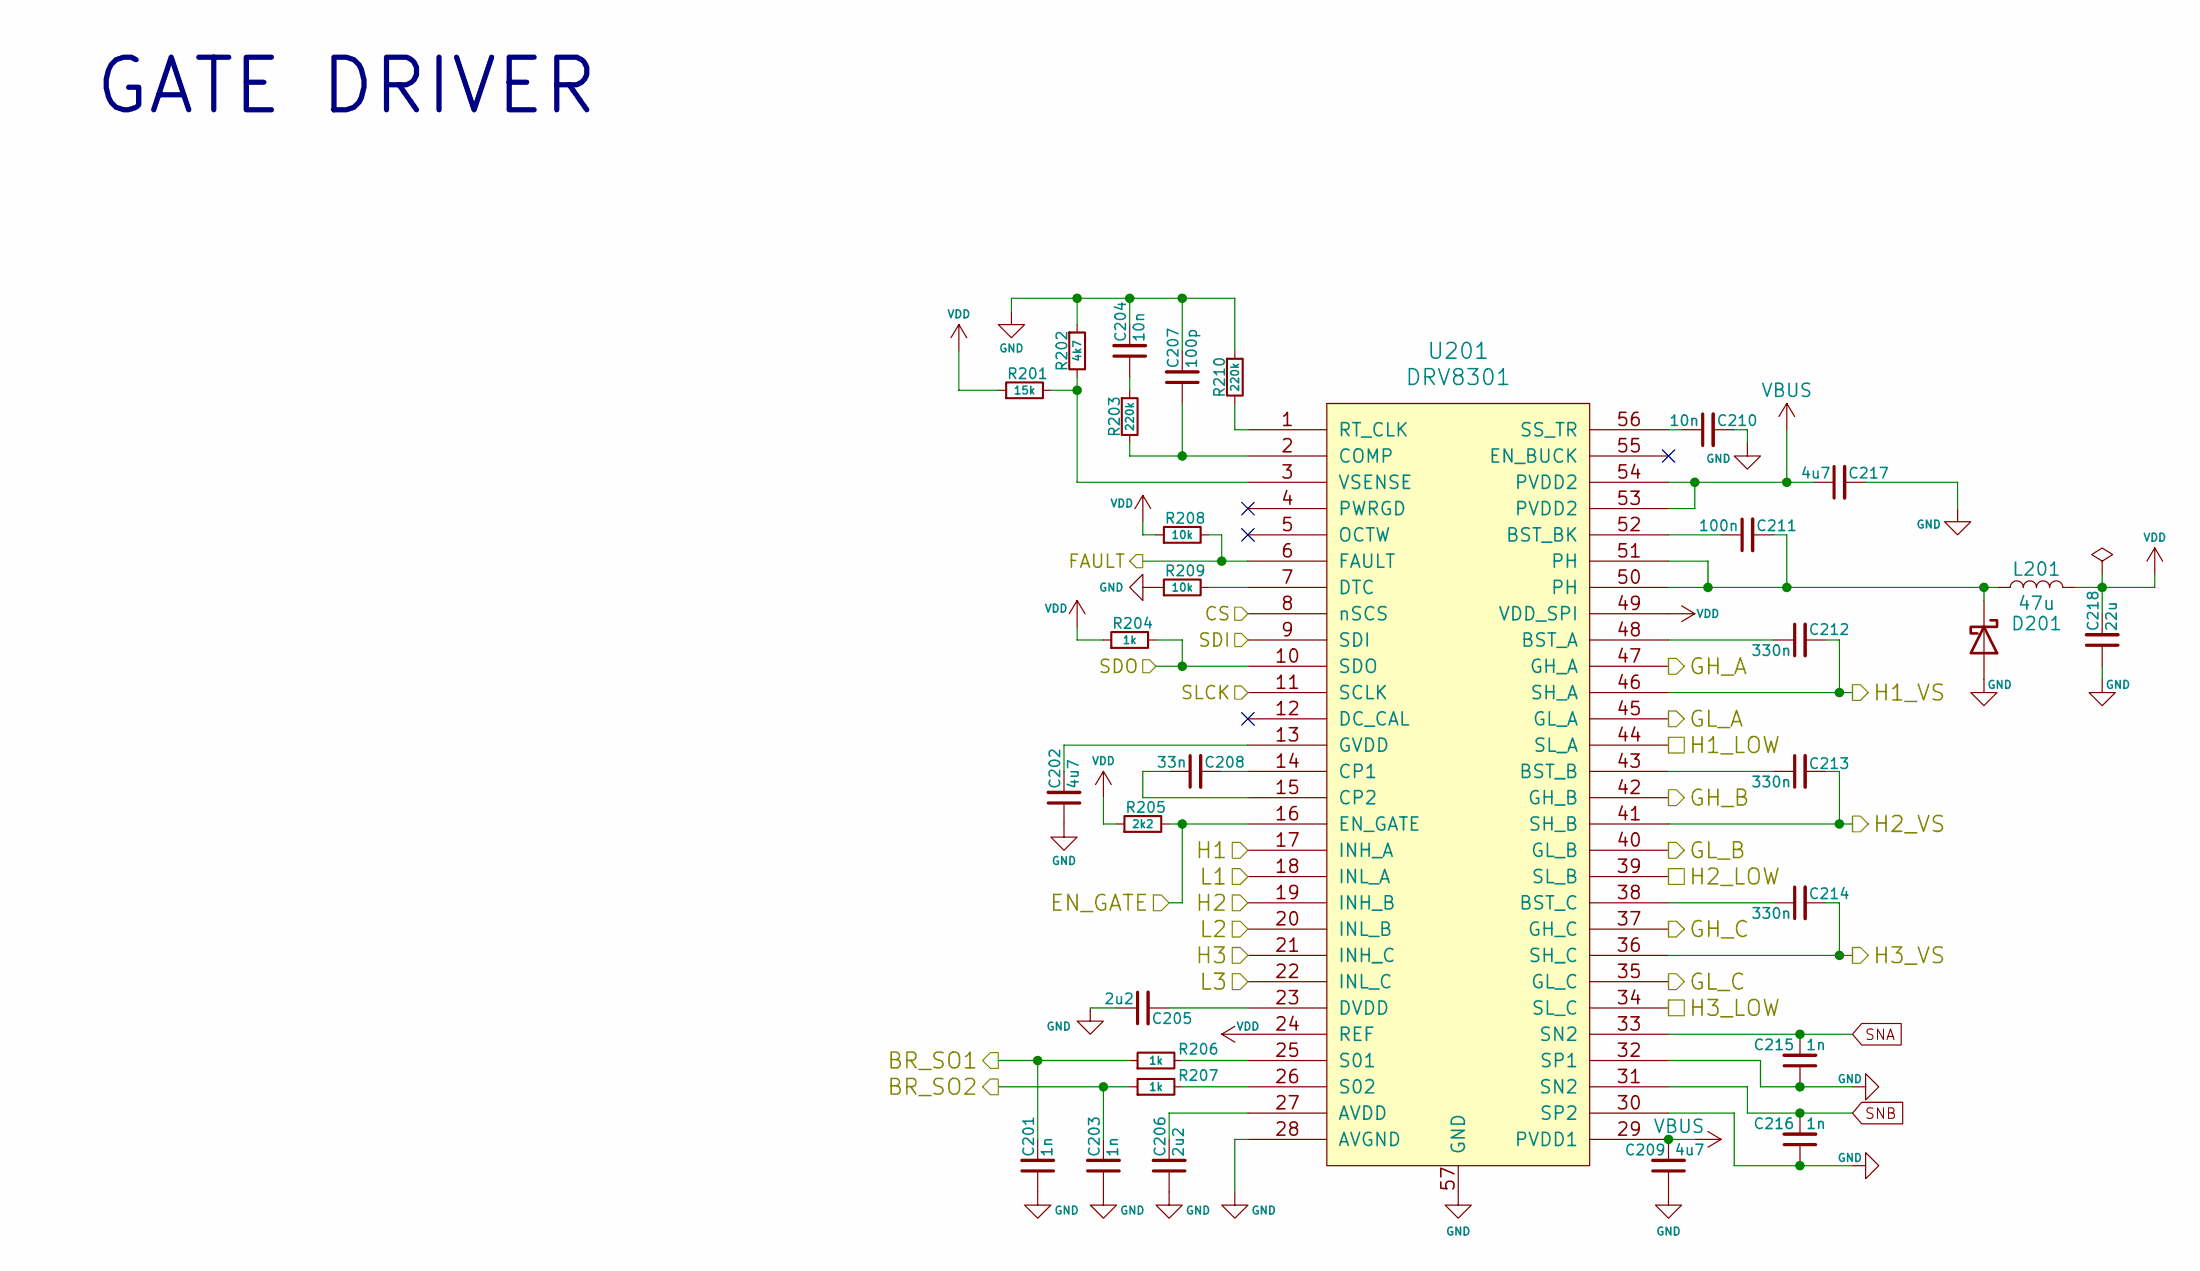
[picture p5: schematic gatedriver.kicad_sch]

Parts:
C201, C203, C215, C216: 1n; C_0402_1005Metric
C202: 4u7; C_1206_3216Metric
C204, C210: 10n; C_0402_1005Metric
C205, C206: 2u2; C_0603_1608Metric
C207: 100p; C_0402_1005Metric
C208: 33n; C_0603_1608Metric
C209, C217: 4u7; C_1210_3225Metric
C211: 100n; C_0603_1608Metric
C212, C213, C214: 330n; C_0603_1608Metric
C218: 22u; C_1210_3225Metric
D201: D_Schottky; D_SOD-123
L201: 47u; L_Changjiang_FXL0630
R201: 15k; R_0402_1005Metric
R202: 4k7; R_0402_1005Metric
R203, R210: 220k; R_0402_1005Metric
R204, R206, R207: 1k; R_0402_1005Metric
R205: 2k2; R_0402_1005Metric
R208, R209: 10k; R_0402_1005Metric
U201: DRV8301; HTSSOP-56_6.1x14-0.5-EP

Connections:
/Gate Driver/BR_SO1: C201.2, R206.1; also elsewhere on the board
/Gate Driver/BR_SO2: C203.2, R207.1; also elsewhere on the board
/Gate Driver/CS: U201.8 (nSCS); also elsewhere on the board
/Gate Driver/EN_GATE: R205.2, U201.16 (EN_GATE); also elsewhere on the board
/Gate Driver/FAULT: R208.2, U201.6 (FAULT); also elsewhere on the board
/Gate Driver/GH_A: U201.47 (GH_A); also elsewhere on the board
/Gate Driver/GH_B: U201.42 (GH_B); also elsewhere on the board
/Gate Driver/GH_C: U201.37 (GH_C); also elsewhere on the board
/Gate Driver/GL_A: U201.45 (GL_A); also elsewhere on the board
/Gate Driver/GL_B: U201.40 (GL_B); also elsewhere on the board
/Gate Driver/GL_C: U201.35 (GL_C); also elsewhere on the board
/Gate Driver/H1: U201.17 (INH_A); also elsewhere on the board
/Gate Driver/H2: U201.19 (INH_B); also elsewhere on the board
/Gate Driver/H3: U201.21 (INH_C); also elsewhere on the board
/Gate Driver/H3_LOW: U201.34 (SL_C); also elsewhere on the board
/Gate Driver/L1: U201.18 (INL_A); also elsewhere on the board
/Gate Driver/L2: U201.20 (INL_B); also elsewhere on the board
/Gate Driver/L3: U201.22 (INL_C); also elsewhere on the board
/Gate Driver/SDI: U201.9 (SDI); also elsewhere on the board
/Gate Driver/SDO: R204.2, U201.10 (SDO); also elsewhere on the board
/Gate Driver/SLCK: U201.11 (SCLK); also elsewhere on the board
/PHASEA: C212.2, U201.46 (SH_A); also elsewhere on the board
/PHASEB: C213.2, U201.41 (SH_B); also elsewhere on the board
/PHASEC: C214.2, U201.36 (SH_C); also elsewhere on the board
GND: C201.1, C202.1, C203.1, C204.2, C205.1, C206.1, C207.2, C209.1, C210.2, C215.1, C216.1, C217.2, C218.1, D201.2 (A), R202.1, R209.1, R210.1, U201.28 (AVGND), U201.30 (SP2), U201.32 (SP1), U201.57 (GND); also elsewhere on the board
unnamed: C204.1, R203.1
unnamed: C211.2, D201.1 (K), L201.1, U201.50 (PH), U201.51 (PH)
unnamed: C206.2, U201.27 (AVDD)
unnamed: C212.1, U201.48 (BST_A)
unnamed: C213.1, U201.43 (BST_B)
unnamed: C211.1, U201.52 (BST_BK)
unnamed: C214.1, U201.38 (BST_C)
unnamed: C207.1, R203.2, U201.2 (COMP)
unnamed: C208.2, U201.14 (CP1)
unnamed: C208.1, U201.15 (CP2)
unnamed: R209.2, U201.7 (DTC)
unnamed: C205.2, U201.23 (DVDD)
unnamed: C202.2, U201.13 (GVDD)
unnamed: R210.2, U201.1 (RT_CLK)
unnamed: R206.2, U201.25 (S01)
unnamed: R207.2, U201.26 (S02)
unnamed: C210.1, U201.56 (SS_TR)
unnamed: R201.2, R202.2, U201.3 (VSENSE)
SNA: C215.2, U201.33 (SN2), U201.44 (SL_A); also elsewhere on the board
SNB: C216.2, U201.31 (SN2), U201.39 (SL_B); also elsewhere on the board
VBUS: C209.2, C217.1, U201.29 (PVDD1), U201.53 (PVDD2), U201.54 (PVDD2); also elsewhere on the board
VDD: C218.2, L201.2, R201.1, R204.1, R205.1, R208.1, U201.24 (REF), U201.49 (VDD_SPI); also elsewhere on the board

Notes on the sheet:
GATE DRIVER

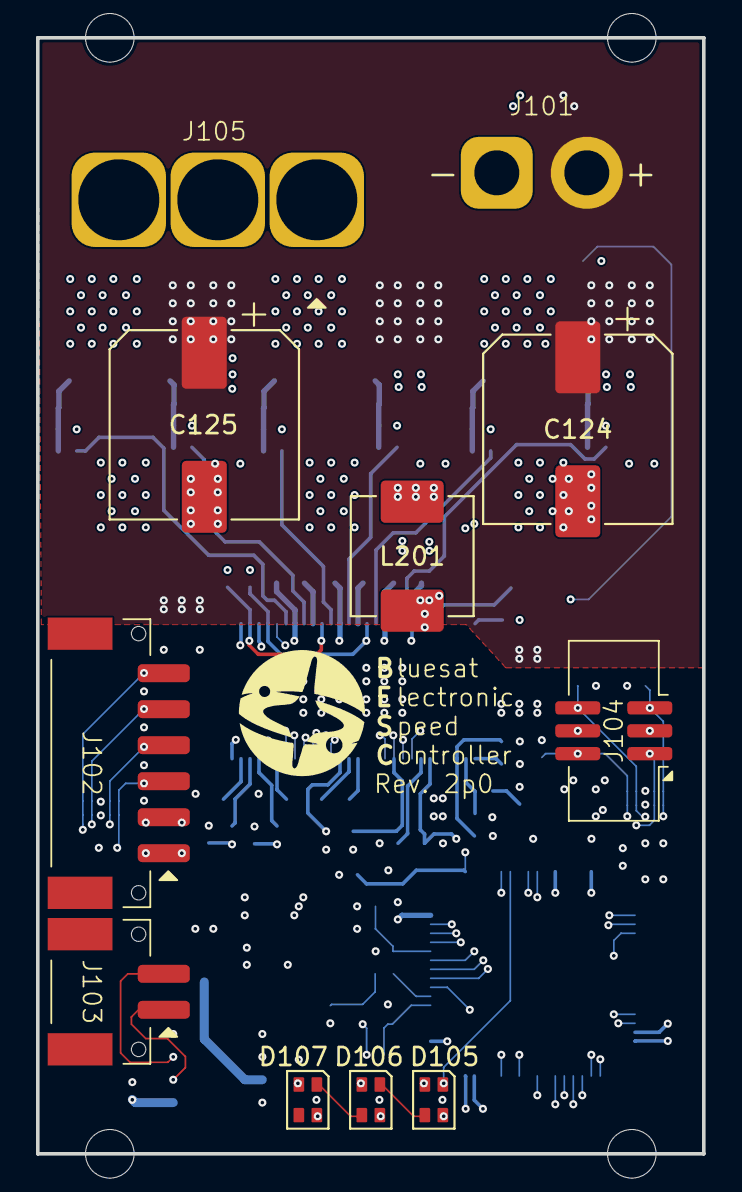
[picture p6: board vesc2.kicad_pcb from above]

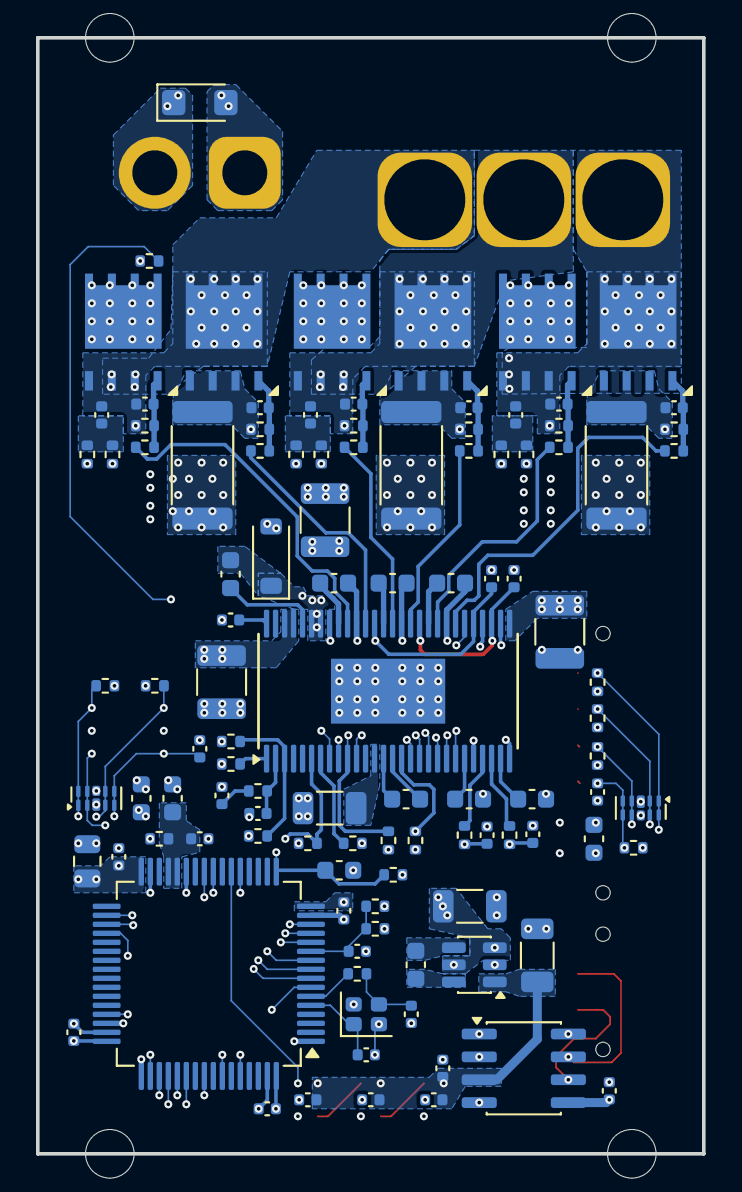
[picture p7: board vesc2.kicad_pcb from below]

Board: 6 copper layers, 37.0 x 62.0 mm, 123 parts (108 on the bottom side), 80 nets.

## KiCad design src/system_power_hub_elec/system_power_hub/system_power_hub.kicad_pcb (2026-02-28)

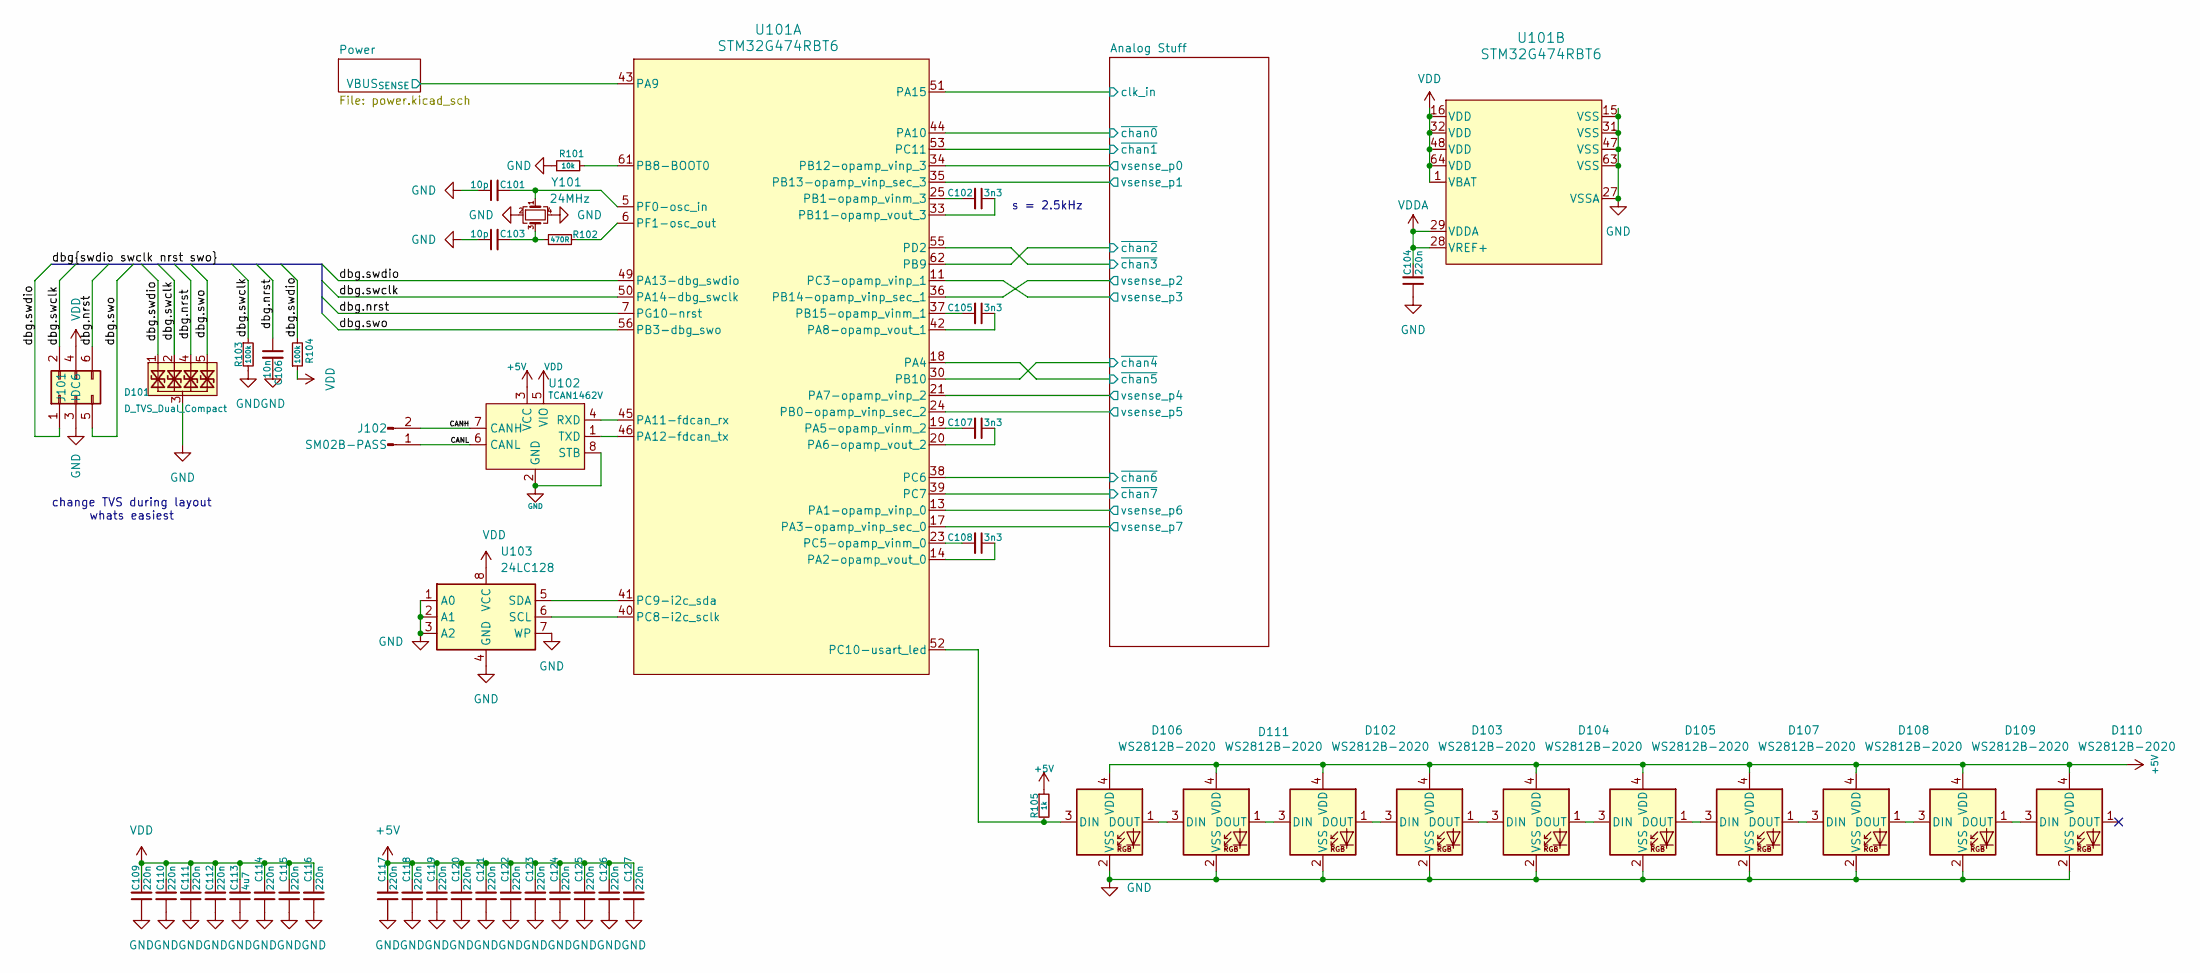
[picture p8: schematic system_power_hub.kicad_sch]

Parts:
C101, C103: 10p; C_0402_1005Metric
C102, C105, C107, C108: 3n3; C_0402_1005Metric
C104, C109, C110, C111, C112, C114, C115, C116, C117, C118, C119, C120, C121, C122, C123, C124, C125, C126, C127: 220n; C_0402_1005Metric
C106: 10n; C_0402_1005Metric
C113: 4u7; C_0805_2012Metric
D101: D_TVS_Dual_Compact; Diodes_UDFN-10_1x2.5mm_P0.5mm
D102, D103, D104, D105, D106, D107, D108, D109, D110, D111: WS2812B-2020
J101: IDC6
J102: SM02B-PASS
R101: 10k; R_0402_1005Metric
R102: 470R; R_0402_1005Metric
R103, R104: 100k; R_0402_1005Metric
R105: 1k; R_0402_1005Metric
U101: STM32G474RBT6; LQFP-64-0.5
U102: TCAN1462V; SOIC-8_3.9x4.9mm_P1.27mm
U103: 24LC128; TSSOP-8_4.4x3mm_P0.65mm
Y101: 24MHz; Crystal_SMD_2016-4Pin_2.0x1.6mm

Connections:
+5V: C117.2, C118.2, C119.2, C120.2, C121.2, C122.2, C123.2, C124.2, C125.2, C126.2, C127.2, D102.4 (VDD), D103.4 (VDD), D104.4 (VDD), D105.4 (VDD), D106.4 (VDD), D107.4 (VDD), D108.4 (VDD), D109.4 (VDD), D110.4 (VDD), D111.4 (VDD), R105.1, U102.3 (VCC); also elsewhere on the board
/Analog Stuff/clk_in: U101.51 (PA15); also elsewhere on the board
/Analog Stuff/vsense_p0: U101.34 (PB12-opamp_vinp_3); also elsewhere on the board
/Analog Stuff/vsense_p1: U101.35 (PB13-opamp_vinp_sec_3); also elsewhere on the board
/Analog Stuff/vsense_p2: U101.36 (PB14-opamp_vinp_sec_1); also elsewhere on the board
/Analog Stuff/vsense_p3: U101.11 (PC3-opamp_vinp_1); also elsewhere on the board
/Analog Stuff/vsense_p4: U101.21 (PA7-opamp_vinp_2); also elsewhere on the board
/Analog Stuff/vsense_p5: U101.24 (PB0-opamp_vinp_sec_2); also elsewhere on the board
/Analog Stuff/vsense_p6: U101.13 (PA1-opamp_vinp_0); also elsewhere on the board
/Analog Stuff/vsense_p7: U101.17 (PA3-opamp_vinp_sec_0); also elsewhere on the board
/Analog Stuff/~chan0: U101.44 (PA10); also elsewhere on the board
/Analog Stuff/~chan1: U101.53 (PC11); also elsewhere on the board
/Analog Stuff/~chan2: U101.62 (PB9); also elsewhere on the board
/Analog Stuff/~chan3: U101.55 (PD2); also elsewhere on the board
/Analog Stuff/~chan4: U101.30 (PB10); also elsewhere on the board
/Analog Stuff/~chan5: U101.18 (PA4); also elsewhere on the board
/Analog Stuff/~chan6: U101.38 (PC6); also elsewhere on the board
/Analog Stuff/~chan7: U101.39 (PC7); also elsewhere on the board
/CANH: J102.2, U102.7 (CANH)
/CANL: J102.1, U102.6 (CANL)
/Power/VBUS_{SENSE}: U101.43 (PA9); also elsewhere on the board
/dbg.nrst: C106.1, D101.4, D101.7, J101.6, U101.7 (PG10-nrst)
/dbg.swclk: D101.2, D101.9, J101.2, R103.1, U101.50 (PA14-dbg_swclk)
/dbg.swdio: D101.1, D101.10, J101.1, R104.2, U101.49 (PA13-dbg_swdio)
/dbg.swo: D101.5, D101.6, J101.5, U101.56 (PB3-dbg_swo)
GND: C101.1, C103.1, C104.1, C106.2, C109.1, C110.1, C111.1, C112.1, C113.1, C114.1, C115.1, C116.1, C117.1, C118.1, C119.1, C120.1, C121.1, C122.1, C123.1, C124.1, C125.1, C126.1, C127.1, D101.3, D101.8, D102.2 (VSS), D103.2 (VSS), D104.2 (VSS), D105.2 (VSS), D106.2 (VSS), D107.2 (VSS), D108.2 (VSS), D109.2 (VSS), D110.2 (VSS), D111.2 (VSS), J101.3, R101.1, R103.2, U101.15 (VSS), U101.27 (VSSA), U101.31 (VSS), U101.47 (VSS), U101.63 (VSS), U102.2 (GND), U102.8 (STB), U102.9 (EP), U103.1 (A0), U103.2 (A1), U103.3 (A2), U103.4 (GND), U103.7 (WP), Y101.2, Y101.4; also elsewhere on the board
unnamed: C103.2, R102.1, Y101.3
unnamed: D102.3 (DIN), D111.1 (DOUT)
unnamed: D102.1 (DOUT), D103.3 (DIN)
unnamed: D103.1 (DOUT), D104.3 (DIN)
unnamed: D104.1 (DOUT), D105.3 (DIN)
unnamed: D105.1 (DOUT), D107.3 (DIN)
unnamed: D106.3 (DIN), R105.2, U101.52 (PC10-usart_led)
unnamed: D106.1 (DOUT), D111.3 (DIN)
unnamed: D107.1 (DOUT), D108.3 (DIN)
unnamed: D108.1 (DOUT), D109.3 (DIN)
unnamed: D109.1 (DOUT), D110.3 (DIN)
unnamed: C108.1, U101.14 (PA2-opamp_vout_0)
unnamed: C107.2, U101.19 (PA5-opamp_vinm_2)
unnamed: C107.1, U101.20 (PA6-opamp_vout_2)
unnamed: C105.1, U101.42 (PA8-opamp_vout_1)
unnamed: U101.45 (PA11-fdcan_rx), U102.4 (RXD)
unnamed: U101.46 (PA12-fdcan_tx), U102.1 (TXD)
unnamed: C102.2, U101.25 (PB1-opamp_vinm_3)
unnamed: R101.2, U101.61 (PB8-BOOT0)
unnamed: C102.1, U101.33 (PB11-opamp_vout_3)
unnamed: C105.2, U101.37 (PB15-opamp_vinm_1)
unnamed: C108.2, U101.23 (PC5-opamp_vinm_0)
unnamed: U101.40 (PC8-i2c_sclk), U103.6 (SCL)
unnamed: U101.41 (PC9-i2c_sda), U103.5 (SDA)
unnamed: C101.2, U101.5 (PF0-osc_in), Y101.1
unnamed: R102.2, U101.6 (PF1-osc_out)
VDD: C109.2, C110.2, C111.2, C112.2, C113.2, C114.2, C115.2, C116.2, J101.4, R104.1, U101.1 (VBAT), U101.16 (VDD), U101.32 (VDD), U101.48 (VDD), U101.64 (VDD), U102.5 (VIO), U103.8 (VCC); also elsewhere on the board
VDDA: C104.2, U101.28 (VREF+), U101.29 (VDDA); also elsewhere on the board

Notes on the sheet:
s = 2.5kHz
change TVS during layout whats easiest

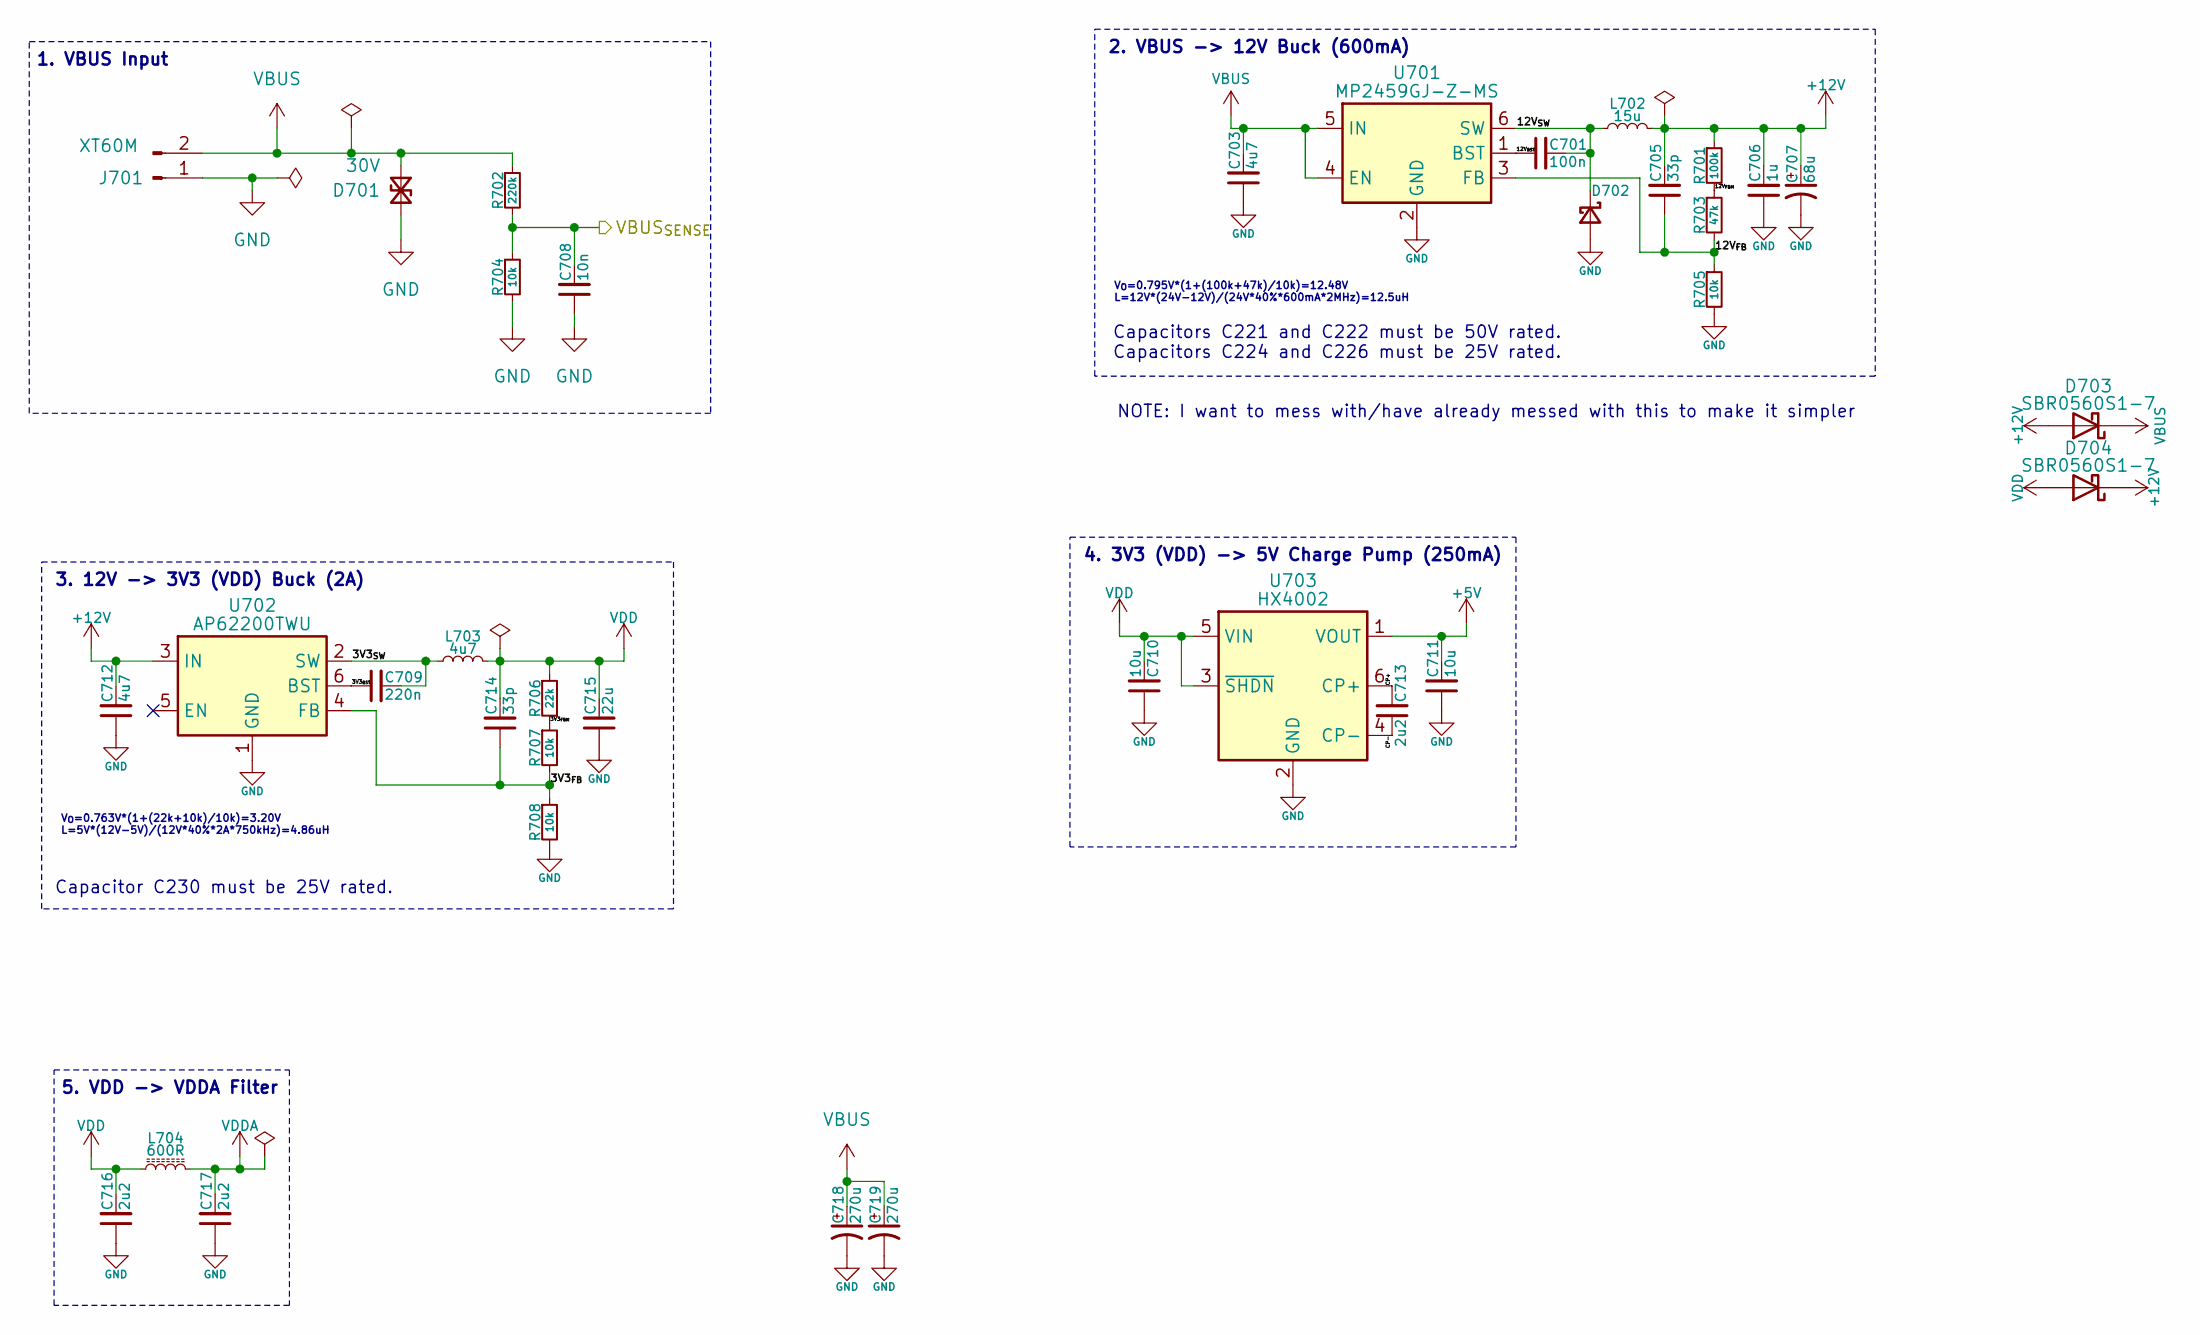
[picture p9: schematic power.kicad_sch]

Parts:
C701: 100n; C_0402_1005Metric
C703: 4u7; C_1210_3225Metric
C705, C714: 33p; C_0402_1005Metric
C706: 1u; C_0805_2012Metric
C707: 68u; CP_Elec_6.3x7.7
C708: 10n; C_0402_1005Metric
C709: 220n; C_0402_1005Metric
C710, C711: 10u; C_1206_3216Metric
C712: 4u7; C_1206_3216Metric
C713, C716, C717: 2u2; C_0603_1608Metric
C715: 22u; C_1210_3225Metric
C718, C719: 270u; CP_Elec_10x10
D701: 30V; D_SMF
D702: D_Schottky_Small; D_SOD-123
D703, D704: SBR0560S1-7; D_SOD-882
J701: XT60M; AMASS_XT60PW-M_1x02_P7.20mm_Horizontal
L702: 15u; L_Changjiang_FNR5040S
L703: 4u7; L_Changjiang_FNR4020S
L704: 600R; R_0402_1005Metric
R701: 100k; R_0402_1005Metric
R702: 220k; R_0402_1005Metric
R703: 47k; R_0402_1005Metric
R704, R705, R707, R708: 10k; R_0402_1005Metric
R706: 22k; R_0402_1005Metric
U701: MP2459GJ-Z-MS; TSOT-23-6
U702: AP62200TWU; TSOT-23-6
U703: HX4002; SOT-23-6

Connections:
+5V: C711.2, U703.1 (VOUT); also elsewhere on the board
+12V: C705.2, C706.2, C707.1, C712.2, D703.2 (A), D704.1 (K), L702.1, R701.1, U702.3 (IN); also elsewhere on the board
/Power/3V3_{BST}: C709.1, U702.6 (BST)
/Power/3V3_{FBM}: R706.2, R707.1
/Power/3V3_{FB}: C714.1, R707.2, R708.1, U702.4 (FB)
/Power/3V3_{SW}: C709.2, L703.1, U702.2 (SW)
/Power/12V_{BST}: C701.1, U701.1 (BST)
/Power/12V_{FBM}: R701.2, R703.1
/Power/12V_{FB}: C705.1, R703.2, R705.1, U701.3 (FB)
/Power/12V_{SW}: C701.2, D702.1 (K), L702.2, U701.6 (SW)
/Power/CP+: C713.2, U703.6 (CP+)
/Power/CP-: C713.1, U703.4 (CP-)
/Power/VBUS_{SENSE}: C708.2, R702.2, R704.1; also elsewhere on the board
GND: C703.1, C706.1, C707.2, C708.1, C710.1, C711.1, C712.1, C715.1, C716.1, C717.1, C718.2, C719.2, D701.2 (A2), D702.2 (A), J701.1, R704.2, R705.2, R708.2, U701.2 (GND), U702.1 (GND), U703.2 (GND); also elsewhere on the board
VBUS: C703.2, C718.1, C719.1, D701.1 (A1), D703.1 (K), J701.2, R702.1, U701.4 (EN), U701.5 (IN); also elsewhere on the board
VDD: C710.2, C714.2, C715.2, C716.2, D704.2 (A), L703.2, L704.1, R706.1, U703.3 (~SHDN), U703.5 (VIN); also elsewhere on the board
VDDA: C717.2, L704.2; also elsewhere on the board

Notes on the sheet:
4. 3V3 (VDD) -> 5V Charge Pump (250mA)
Capacitor C230 must be 25V rated.
1. VBUS Input
V_{O}=0.795V*(1+(100k+47k)/10k)=12.48V L=12V*(24V-12V)/(24V*40%*600mA*2MHz)=12.5uH
2. VBUS -> 12V Buck (600mA)
Capacitors C221 and C222 must be 50V rated. Capacitors C224 and C226 must be 25V rated.
NOTE: I want to mess with/have already messed with this to make it simpler
5. VDD -> VDDA Filter
3. 12V -> 3V3 (VDD) Buck (2A)
V_{O}=0.763V*(1+(22k+10k)/10k)=3.20V L=5V*(12V-5V)/(12V*40%*2A*750kHz)=4.86uH

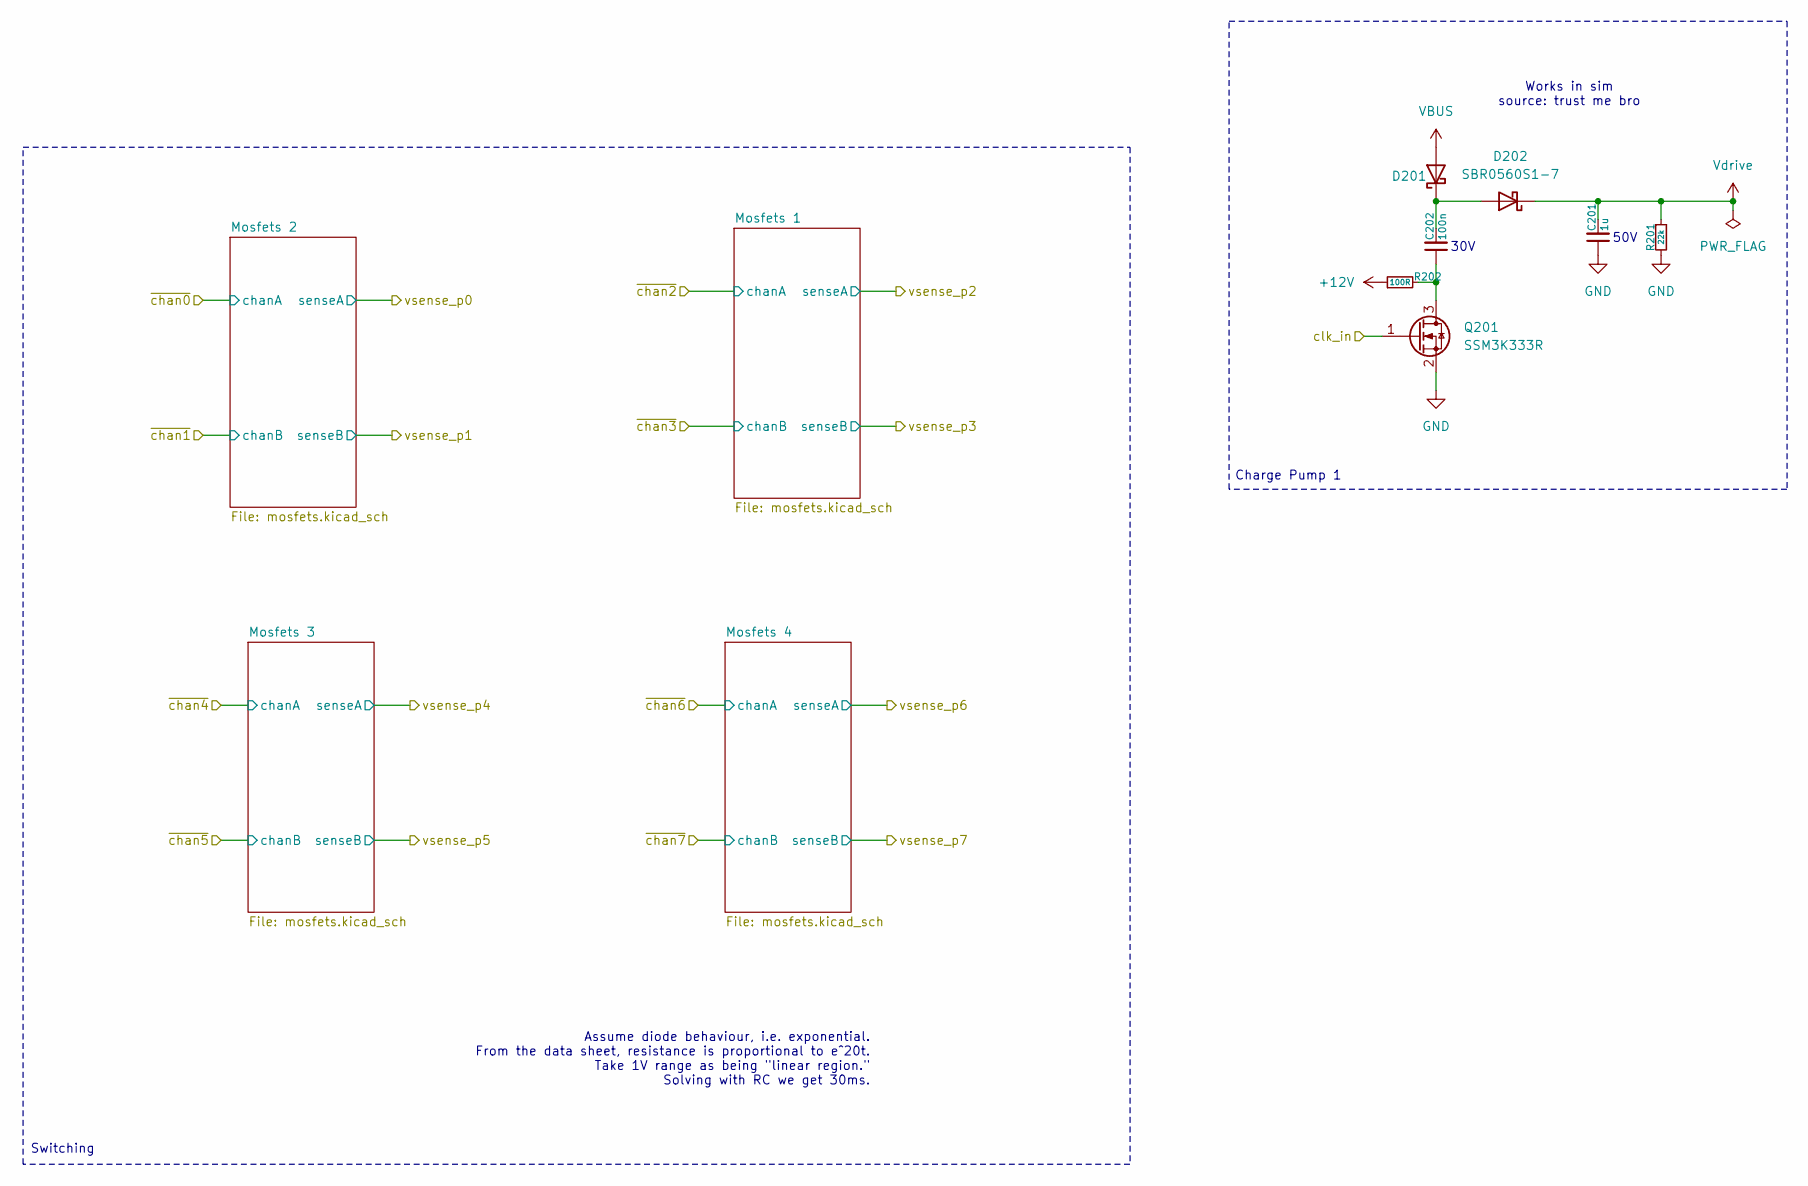
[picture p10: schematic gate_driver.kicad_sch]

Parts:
C201: 1u; C_1206_3216Metric
C202: 100n; C_0603_1608Metric
D201, D202: SBR0560S1-7; D_SOD-882
Q201: SSM3K333R; SOT-23-3
R201: 22k; R_0402_1005Metric
R202: 100R; R_0402_1005Metric

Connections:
+12V: R202.1; also elsewhere on the board
/Analog Stuff/clk_in: Q201.1 (G); also elsewhere on the board
GND: C201.1, Q201.2 (S), R201.2; also elsewhere on the board
unnamed: C202.2, D201.1 (K), D202.2 (A)
unnamed: C202.1, Q201.3 (D), R202.2
VBUS: D201.2 (A); also elsewhere on the board
Vdrive: C201.2, D202.1 (K), R201.1; also elsewhere on the board

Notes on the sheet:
Switching
50V
Charge Pump 1
Assume diode behaviour, i.e. exponential. From the data sheet, resistance is proportional to e^20t. Take 1V range as being "linear region." Solving with RC we get 30ms.
Works in sim source: trust me bro
30V

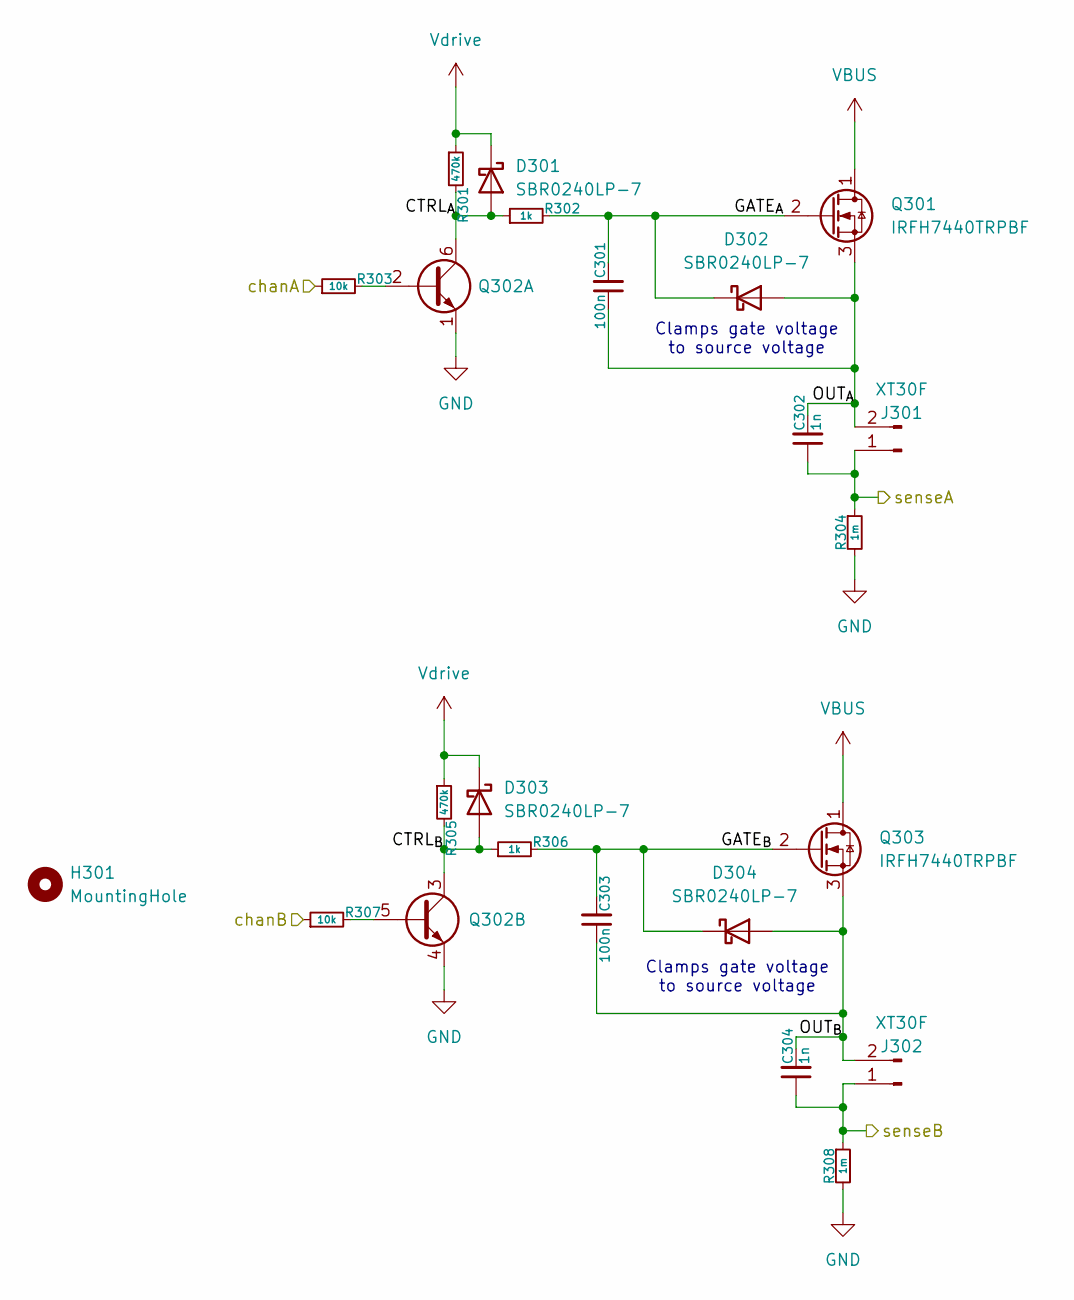
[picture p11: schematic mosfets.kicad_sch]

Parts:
C301, C303: 100n; C_0402_1005Metric
C302, C304: 1n; C_0402_1005Metric
D301, D302, D303, D304: SBR0240LP-7; D_SOD-882
H301: MountingHole; M2.5_Internal
J301, J302: XT30F; AMASS_XT30PW-F_1x02_P2.50mm_Horizontal
Q301, Q303: IRFH7440TRPBF; PQFN_5x6mm_E_DGS
Q302: Q_Dual_NPN_NPN_E1B1C2E2B2C1; SOT-363
R301, R305: 470k; R_0402_1005Metric
R302, R306: 1k; R_0402_1005Metric
R303, R307: 10k; R_0402_1005Metric
R304, R308: 1m; R_2512_6332Metric

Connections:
/Analog Stuff/Mosfets 1/CTRL_{A}: D301.2 (A), Q302.6 (C1), R301.2, R302.1
/Analog Stuff/Mosfets 1/CTRL_{B}: D303.2 (A), Q302.3 (C2), R305.2, R306.1
/Analog Stuff/Mosfets 1/GATE_{A}: C301.2, D302.1 (K), Q301.2 (G), R302.2
/Analog Stuff/Mosfets 1/GATE_{B}: C303.2, D304.1 (K), Q303.2 (G), R306.2
/Analog Stuff/Mosfets 1/OUT_{A}: C301.1, C302.2, D302.2 (A), J301.2, Q301.3 (S)
/Analog Stuff/Mosfets 1/OUT_{B}: C303.1, C304.2, D304.2 (A), J302.2, Q303.3 (S)
/Analog Stuff/vsense_p2: C302.1, J301.1, R304.1; also elsewhere on the board
/Analog Stuff/vsense_p3: C304.1, J302.1, R308.1; also elsewhere on the board
/Analog Stuff/~chan2: R303.1; also elsewhere on the board
/Analog Stuff/~chan3: R307.1; also elsewhere on the board
GND: Q302.1 (E1), Q302.4 (E2), R304.2, R308.2; also elsewhere on the board
unnamed: Q302.2 (B1), R303.2
unnamed: Q302.5 (B2), R307.2
VBUS: Q301.1 (D), Q303.1 (D); also elsewhere on the board
Vdrive: D301.1 (K), D303.1 (K), R301.1, R305.1; also elsewhere on the board

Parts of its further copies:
C401, C403, C501, C503, C601, C603: 100n; C_0402_1005Metric
C402, C404, C502, C504, C602, C604: 1n; C_0402_1005Metric
D401, D402, D403, D404, D501, D502, D503, D504, D601, D602, D603, D604: SBR0240LP-7; D_SOD-882
H401, H501, H601: MountingHole; M2.5_Internal
J401, J402, J501, J502, J601, J602: XT30F; AMASS_XT30PW-F_1x02_P2.50mm_Horizontal
Q401, Q403, Q501, Q503, Q601, Q603: IRFH7440TRPBF; PQFN_5x6mm_E_DGS
Q402, Q502, Q602: Q_Dual_NPN_NPN_E1B1C2E2B2C1; SOT-363
R401, R405, R501, R505, R601, R605: 470k; R_0402_1005Metric
R402, R406, R502, R506, R602, R606: 1k; R_0402_1005Metric
R403, R407, R503, R507, R603, R607: 10k; R_0402_1005Metric
R404, R408, R504, R508, R604, R608: 1m; R_2512_6332Metric

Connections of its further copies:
/Analog Stuff/Mosfets 2/CTRL_{A}: D401.2 (A), Q402.6 (C1), R401.2, R402.1
/Analog Stuff/Mosfets 2/CTRL_{B}: D403.2 (A), Q402.3 (C2), R405.2, R406.1
/Analog Stuff/Mosfets 2/GATE_{A}: C401.2, D402.1 (K), Q401.2 (G), R402.2
/Analog Stuff/Mosfets 2/GATE_{B}: C403.2, D404.1 (K), Q403.2 (G), R406.2
/Analog Stuff/Mosfets 2/OUT_{A}: C401.1, C402.2, D402.2 (A), J401.2, Q401.3 (S)
/Analog Stuff/Mosfets 2/OUT_{B}: C403.1, C404.2, D404.2 (A), J402.2, Q403.3 (S)
/Analog Stuff/Mosfets 3/CTRL_{A}: D501.2 (A), Q502.6 (C1), R501.2, R502.1
/Analog Stuff/Mosfets 3/CTRL_{B}: D503.2 (A), Q502.3 (C2), R505.2, R506.1
/Analog Stuff/Mosfets 3/GATE_{A}: C501.2, D502.1 (K), Q501.2 (G), R502.2
/Analog Stuff/Mosfets 3/GATE_{B}: C503.2, D504.1 (K), Q503.2 (G), R506.2
/Analog Stuff/Mosfets 3/OUT_{A}: C501.1, C502.2, D502.2 (A), J501.2, Q501.3 (S)
/Analog Stuff/Mosfets 3/OUT_{B}: C503.1, C504.2, D504.2 (A), J502.2, Q503.3 (S)
/Analog Stuff/Mosfets 4/CTRL_{A}: D601.2 (A), Q602.6 (C1), R601.2, R602.1
/Analog Stuff/Mosfets 4/CTRL_{B}: D603.2 (A), Q602.3 (C2), R605.2, R606.1
/Analog Stuff/Mosfets 4/GATE_{A}: C601.2, D602.1 (K), Q601.2 (G), R602.2
/Analog Stuff/Mosfets 4/GATE_{B}: C603.2, D604.1 (K), Q603.2 (G), R606.2
/Analog Stuff/Mosfets 4/OUT_{A}: C601.1, C602.2, D602.2 (A), J601.2, Q601.3 (S)
/Analog Stuff/Mosfets 4/OUT_{B}: C603.1, C604.2, D604.2 (A), J602.2, Q603.3 (S)
/Analog Stuff/vsense_p0: C402.1, J401.1, R404.1; also elsewhere on the board
/Analog Stuff/vsense_p1: C404.1, J402.1, R408.1; also elsewhere on the board
/Analog Stuff/vsense_p4: C502.1, J501.1, R504.1; also elsewhere on the board
/Analog Stuff/vsense_p5: C504.1, J502.1, R508.1; also elsewhere on the board
/Analog Stuff/vsense_p6: C602.1, J601.1, R604.1; also elsewhere on the board
/Analog Stuff/vsense_p7: C604.1, J602.1, R608.1; also elsewhere on the board
/Analog Stuff/~chan0: R403.1; also elsewhere on the board
/Analog Stuff/~chan1: R407.1; also elsewhere on the board
/Analog Stuff/~chan4: R503.1; also elsewhere on the board
/Analog Stuff/~chan5: R507.1; also elsewhere on the board
/Analog Stuff/~chan6: R603.1; also elsewhere on the board
/Analog Stuff/~chan7: R607.1; also elsewhere on the board
GND: Q402.1 (E1), Q402.4 (E2), Q502.1 (E1), Q502.4 (E2), Q602.1 (E1), Q602.4 (E2), R404.2, R408.2, R504.2, R508.2, R604.2, R608.2; also elsewhere on the board
unnamed: Q402.2 (B1), R403.2
unnamed: Q402.5 (B2), R407.2
unnamed: Q502.2 (B1), R503.2
unnamed: Q502.5 (B2), R507.2
unnamed: Q602.2 (B1), R603.2
unnamed: Q602.5 (B2), R607.2
VBUS: Q401.1 (D), Q403.1 (D), Q501.1 (D), Q503.1 (D), Q601.1 (D), Q603.1 (D); also elsewhere on the board
Vdrive: D401.1 (K), D403.1 (K), D501.1 (K), D503.1 (K), D601.1 (K), D603.1 (K), R401.1, R405.1, R501.1, R505.1, R601.1, R605.1; also elsewhere on the board

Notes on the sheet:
Clamps gate voltage to source voltage

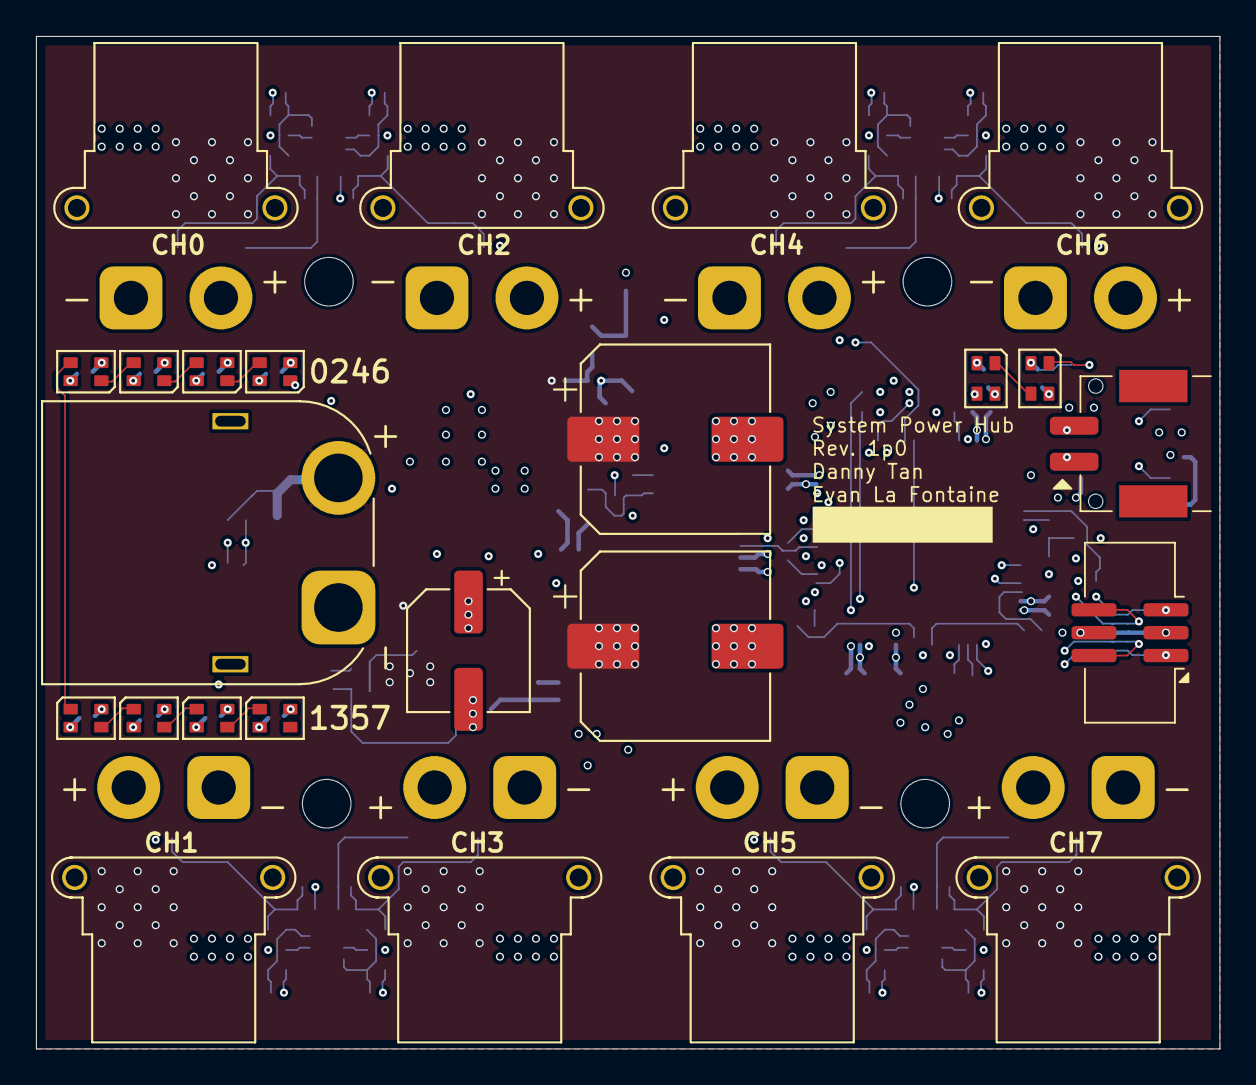
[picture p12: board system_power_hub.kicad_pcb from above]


Board: 6 copper layers, 65.8 x 56.2 mm, 180 parts (152 on the bottom side), 101 nets.

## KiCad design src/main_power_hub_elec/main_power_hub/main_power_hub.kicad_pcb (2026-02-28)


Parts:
C1, C2, C3, C4, C5, C6, C23, C24, C25, C26, C27, C28, C29, C30: 220n; C_0402_1005Metric
C7: 4u7; C_0805_2012Metric
C11, C15, C32, C33: 100p; C_0402_1005Metric
C13, C14: 10p; C_0402_1005Metric
C20: 10n; C_0402_1005Metric
D1, D2, D13, D14, D15, D16: WS2812B-2020
D401: 3V3; Diodes_UDFN-10_1x2.5mm_P0.5mm
H1, H2, H3: MountingHole; M2.5_Internal
J6: IDC6
J101: SM02B-PASS
R2: 470R; R_0402_1005Metric
R13: 10k; R_0402_1005Metric
R14, R15: 100k; R_0402_1005Metric
R17: 1k; R_0402_1005Metric
U2: STM32G474RBT6; LQFP-64-0.5
U4: 24LC128; TSSOP-8_4.4x3.0-0.65
U102: TCAN1462V; SOIC-8_3.9x4.9mm_P1.27mm
Y1: 24MHz; Crystal_SMD_2016-4Pin_2.0x1.6mm

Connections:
+5V: C2.2, C25.2, C26.2, C27.2, C28.2, C29.2, C30.2, D1.4 (VDD), D2.4 (VDD), D13.4 (VDD), D14.4 (VDD), D15.4 (VDD), D16.4 (VDD), R17.1, U102.3 (VCC); also elsewhere on the board
/Analog Stuff/clk_in: U2.60 (PB7-cp_pulse_gen); also elsewhere on the board
/Analog Stuff/vsense_p0: U2.13 (PA1-opamp_vinp_0); also elsewhere on the board
/Analog Stuff/vsense_p1: U2.21 (PA7-opamp_vinp_1); also elsewhere on the board
/Analog Stuff/vsense_p2: U2.33 (PB11-opamp_vinp_2); also elsewhere on the board
/Analog Stuff/vsense_p3: U2.24 (PB0-opamp_vinp_3); also elsewhere on the board
/Analog Stuff/~chan0: U2.41 (PC9-channel_0); also elsewhere on the board
/Analog Stuff/~chan1: U2.40 (PC8-channel_1); also elsewhere on the board
/Analog Stuff/~chan2: U2.39 (PC7-channel_2); also elsewhere on the board
/Analog Stuff/~chan3: U2.38 (PC6-channel_3); also elsewhere on the board
/CANH: J101.2, U102.7 (CANH)
/CANL: J101.1, U102.6 (CANL)
/Power/VBUS_{SENSE}: U2.36 (PB14-vbus_sense); also elsewhere on the board
/dbg.nrst: C20.1, D401.5, D401.6, J6.2, U2.7 (PG10-nrst)
/dbg.swclk: D401.4, D401.7, J6.6, R15.1, U2.50 (PA14-dbg_swclk)
/dbg.swdio: D401.2, D401.9, J6.5, R14.2, U2.49 (PA13-dbg_swdio)
/dbg.swo: D401.1, D401.10, J6.1, U2.56 (PB3-dbg_swo)
GND: C1.1, C2.1, C3.1, C4.1, C5.1, C6.1, C7.1, C13.1, C14.1, C20.2, C23.1, C24.1, C25.1, C26.1, C27.1, C28.1, C29.1, C30.1, D1.2 (VSS), D2.2 (VSS), D13.2 (VSS), D14.2 (VSS), D15.2 (VSS), D16.2 (VSS), D401.3, D401.8, J6.3, R13.1, R15.2, U2.15 (VSS), U2.27 (VSSA), U2.31 (VSS), U2.47 (VSS), U2.63 (VSS), U4.1 (A0), U4.2 (A1), U4.3 (A2), U4.4 (GND), U4.7 (WP), U102.2 (GND), U102.8 (STB), U102.9 (EP), Y1.2, Y1.4; also elsewhere on the board
unnamed: C14.2, R2.1, Y1.3
unnamed: D1.3 (DIN), R17.2, U2.43 (PA9-usart_led)
unnamed: D1.1 (DOUT), D2.3 (DIN)
unnamed: D2.1 (DOUT), D13.3 (DIN)
unnamed: D13.1 (DOUT), D14.3 (DIN)
unnamed: D14.1 (DOUT), D15.3 (DIN)
unnamed: D15.1 (DOUT), D16.3 (DIN)
unnamed: C32.2, U2.14 (PA2-opamp_vout_0)
unnamed: C33.1, U2.19 (PA5-opamp_vinm_1)
unnamed: C33.2, U2.20 (PA6-opamp_vout_1)
unnamed: U2.51 (PA15-i2c_sclk), U4.6 (SCL)
unnamed: C15.2, U2.25 (PB1-opamp_vout_3)
unnamed: C15.1, U2.26 (PB2-opamp_vinm_3)
unnamed: R13.2, U2.61 (PB8-boot0)
unnamed: U2.62 (PB9-i2c_sda), U4.5 (SDA)
unnamed: C11.1, U2.30 (PB10-opamp_vinm_2)
unnamed: C11.2, U2.34 (PB12-opamp_vout_2)
unnamed: C32.1, U2.23 (PC5-opamp_vinm_0)
unnamed: C13.2, U2.5 (PF0-osc_in), Y1.1
unnamed: R2.2, U2.6 (PF1-osc_out)
unnamed: U2.45 (PA11-fdcan_rx), U102.4 (RXD)
unnamed: U2.46 (PA12-fdcan_tx), U102.1 (TXD)
VDD: C3.2, C4.2, C5.2, C6.2, C7.2, C23.2, C24.2, J6.4, R14.1, U2.1 (VBAT), U2.16 (VDD), U2.32 (VDD), U2.48 (VDD), U2.64 (VDD), U4.8 (VCC), U102.5 (VIO); also elsewhere on the board
VDDA: C1.2, U2.28 (VREF+), U2.29 (VDDA); also elsewhere on the board

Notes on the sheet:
s = 2.5kHz
TVS IS BACK :)


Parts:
C12: 10n; C_0402_1005Metric
C221, C222: 1u; C_1206_3216Metric
C223, C227: 68u; CP_Elec_6.3x7.7
C224: 100n; C_0402_1005Metric
C225, C232: 33p; C_0402_1005Metric
C226: 1u; C_0805_2012Metric
C230: 4u7; C_1206_3216Metric
C231: 220n; C_0402_1005Metric
C233: 22u; C_1210_3225Metric
C240, C242: 10u; C_1206_3216Metric
C241, C250, C251: 2u2; C_0603_1608Metric
C260, C261: 270u; CP_Elec_10x10
D3: 30V; D_SMF
D220: D_Schottky_Small; D_SOD-123
J1: XT90M; AMASS_XT90PW-M_1x02_P10.90mm_Horizontal
L220: 120R; R_0603_1608Metric
L221: 15u; L_Changjiang_FNR5040S
L230: 4u7; L_Changjiang_FNR4020S
L250: 600R; R_0402_1005Metric
R3: 220k; R_0402_1005Metric
R4, R222, R231, R232: 10k; R_0402_1005Metric
R220: 100k; R_0402_1005Metric
R221: 47k; R_0402_1005Metric
R230: 22k; R_0402_1005Metric
U220: MP2459GJ-Z-MS; TSOT-23-6
U230: AP62200TWU; TSOT-23-6
U240: HX4002; SOT-23-6

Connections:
+5V: C242.2, U240.1 (VOUT); also elsewhere on the board
+12V: C225.2, C226.2, C227.1, C230.2, L221.1, R220.1, U230.3 (IN); also elsewhere on the board
/Power/3V3_{BST}: C231.1, U230.6 (BST)
/Power/3V3_{FBM}: R230.2, R231.1
/Power/3V3_{FB}: C232.1, R231.2, R232.1, U230.4 (FB)
/Power/3V3_{SW}: C231.2, L230.1, U230.2 (SW)
/Power/12V_{BST}: C224.1, U220.1 (BST)
/Power/12V_{FBM}: R220.2, R221.1
/Power/12V_{FB}: C225.1, R221.2, R222.1, U220.3 (FB)
/Power/12V_{SW}: C224.2, D220.1 (K), L221.2, U220.6 (SW)
/Power/CP+: C241.2, U240.6 (CP+)
/Power/CP-: C241.1, U240.4 (CP-)
/Power/VBUS_{FLT}: C222.2, C223.1, L220.2, U220.4 (EN), U220.5 (IN)
/Power/VBUS_{SENSE}: C12.2, R3.2, R4.1; also elsewhere on the board
GND: C12.1, C221.1, C222.1, C223.2, C226.1, C227.2, C230.1, C233.1, C240.1, C242.1, C250.1, C251.1, C260.2, C261.2, D3.1 (A1), D220.2 (A), J1.1, R4.2, R222.2, R232.2, U220.2 (GND), U230.1 (GND), U240.2 (GND); also elsewhere on the board
VBUS: C221.2, C260.1, C261.1, D3.2 (A2), J1.2, L220.1, R3.1; also elsewhere on the board
VDD: C232.2, C233.2, C240.2, C250.2, L230.2, L250.1, R230.1, U240.3 (~SHDN), U240.5 (VIN); also elsewhere on the board
VDDA: C251.2, L250.2; also elsewhere on the board

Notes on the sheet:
4. 3V3 (VDD) -> 5V Charge Pump (250mA)
Capacitor C230 must be 25V rated.
1. VBUS Input
V_{O}=0.795V*(1+(100k+47k)/10k)=12.48V L=12V*(24V-12V)/(24V*40%*600mA*2MHz)=12.5uH
Capacitors C221 and C222 must be 50V rated. Capacitors C224 and C226 must be 25V rated.
2. VBUS -> 12V Buck (600mA)
5. VDD -> VDDA Filter
3. 12V -> 3V3 (VDD) Buck (2A)
V_{O}=0.763V*(1+(22k+10k)/10k)=3.20V L=5V*(12V-5V)/(12V*40%*2A*750kHz)=4.86uH


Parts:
C36: 100n; C_0603_1608Metric
C37: 1u; C_1206_3216Metric
D11, D12: SBR0560S1-7; D_SOD-123
J3: SM02B-PASS
Q1: SSM3K333R; SOT-23-3
R8: 100R; R_0402_1005Metric
R19: 22k; R_0402_1005Metric

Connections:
+12V: R8.1; also elsewhere on the board
/Analog Stuff/clk_in: Q1.1 (G); also elsewhere on the board
GND: C37.1, Q1.2 (S), R19.2; also elsewhere on the board
unnamed: C36.2, D11.1 (K), D12.2 (A)
unnamed: C37.2, D12.1 (K), J3.2
unnamed: C36.1, Q1.3 (D), R8.2
VBUS: D11.2 (A); also elsewhere on the board
Vdrive: J3.1, R19.1; also elsewhere on the board

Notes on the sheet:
Switching
Charge Pump
50V
E-Stop, normally closed
Assume diode behaviour, i.e. exponential. From the data sheet, resistance is proportional to e^20t. Take 1V range as being "linear region." Solving with RC we get 30ms.
Works in sim source: trust me bro
30V


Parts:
C8, C9: 100n; C_0603_1608Metric
C10, C19, C22, C31: 1n; C_0402_1005Metric
D4, D6, D8, D10: SBR0240LP-7; D_SOD-882D
J2, J4: XT60F; AMASS_XT60PW-F_1x02_P7.20mm_Horizontal
Q2: Q_Dual_NPN_NPN_E1B1C2E2B2C1; SOT-363
Q3, Q4: IRFH7440TRPBF; PQFN_5x6mm_E_DGS
R5, R6: 10k; R_0402_1005Metric
R7, R9: 470k; R_0402_1005Metric
R10, R11: 1m; R_2512_6332Metric
R18, R24: 1k; R_0402_1005Metric

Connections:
/Analog Stuff/vsense_p2: C10.1, J2.1, R10.1; also elsewhere on the board
/Analog Stuff/vsense_p3: C19.1, J4.1, R11.1; also elsewhere on the board
/Analog Stuff/~chan2: R5.1; also elsewhere on the board
/Analog Stuff/~chan3: R6.1; also elsewhere on the board
GND: C22.2, C31.2, Q2.1 (E1), Q2.4 (E2), R10.2, R11.2; also elsewhere on the board
unnamed: C8.1, C10.2, D4.2 (A), J2.2, Q3.3 (S)
unnamed: C8.2, D4.1 (K), Q3.2 (G), R18.2
unnamed: C9.1, C19.2, D6.2 (A), J4.2, Q4.3 (S)
unnamed: C9.2, D6.1 (K), Q4.2 (G), R24.2
unnamed: D8.2 (A), Q2.6 (C1), R7.2, R18.1
unnamed: D10.2 (A), Q2.3 (C2), R9.2, R24.1
unnamed: Q2.2 (B1), R5.2
unnamed: Q2.5 (B2), R6.2
VBUS: C22.1, C31.1, Q3.1 (D), Q4.1 (D); also elsewhere on the board
Vdrive: D8.1 (K), D10.1 (K), R7.1, R9.1; also elsewhere on the board

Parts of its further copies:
C42, C43: 100n; C_0603_1608Metric
C44, C46, C48, C49: 1n; C_0402_1005Metric
D5, D7, D9, D17: SBR0240LP-7; D_SOD-882D
J8, J9: XT60F; AMASS_XT60PW-F_1x02_P7.20mm_Horizontal
Q8: Q_Dual_NPN_NPN_E1B1C2E2B2C1; SOT-363
Q9, Q10: IRFH7440TRPBF; PQFN_5x6mm_E_DGS
R16, R21: 10k; R_0402_1005Metric
R20, R25: 1k; R_0402_1005Metric
R22, R23: 470k; R_0402_1005Metric
R26, R27: 1m; R_2512_6332Metric

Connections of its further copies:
/Analog Stuff/vsense_p0: C44.1, J8.1, R26.1; also elsewhere on the board
/Analog Stuff/vsense_p1: C46.1, J9.1, R27.1; also elsewhere on the board
/Analog Stuff/~chan0: R16.1; also elsewhere on the board
/Analog Stuff/~chan1: R21.1; also elsewhere on the board
GND: C48.2, C49.2, Q8.1 (E1), Q8.4 (E2), R26.2, R27.2; also elsewhere on the board
unnamed: C42.1, C44.2, D5.2 (A), J8.2, Q9.3 (S)
unnamed: C42.2, D5.1 (K), Q9.2 (G), R20.2
unnamed: C43.1, C46.2, D7.2 (A), J9.2, Q10.3 (S)
unnamed: C43.2, D7.1 (K), Q10.2 (G), R25.2
unnamed: D9.2 (A), Q8.6 (C1), R20.1, R22.2
unnamed: D17.2 (A), Q8.3 (C2), R23.2, R25.1
unnamed: Q8.2 (B1), R16.2
unnamed: Q8.5 (B2), R21.2
VBUS: C48.1, C49.1, Q9.1 (D), Q10.1 (D); also elsewhere on the board
Vdrive: D9.1 (K), D17.1 (K), R22.1, R23.1; also elsewhere on the board

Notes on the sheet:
Clamps gate voltage to source voltage



Board: 6 copper layers, 64.0 x 64.0 mm, 134 parts (113 on the bottom side), 75 nets.

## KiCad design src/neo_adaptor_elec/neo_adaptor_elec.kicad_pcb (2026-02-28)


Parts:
H1: M4 maybe; MountingHole_4.3mm_M4
J1: Real Connector Hours; SM06B-PASS
J2: Solder; SolderWire-0.25sqmm_1x06_P4.2mm_D0.65mm_OD1.7mm

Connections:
/H1/A: J1.4, J2.4
/H2/B: J1.5, J2.5
/H3/A: J1.6, J2.6
/TEMP: J1.3, J2.3
GND: J1.1, J2.1
VDD: J1.2, J2.2


Board: 2 copper layers, 44.0 x 45.0 mm, 3 parts (0 on the bottom side), 6 nets.

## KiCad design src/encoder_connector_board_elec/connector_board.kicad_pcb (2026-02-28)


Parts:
C1: 22u; C_1210_3225Metric
C7: 4u7; C_1210_3225Metric; Rating 50V
C8: 100n; C_0402_1005Metric
C12: 33p; C_0402_1005Metric
D1: D_Schottky_Small; D_SOD-882
D2: D_Schottky_Small; D_SOD-123
H1, H2: M2.5; M2.5_Internal
J1: Conn_02x12_Odd_Even; BM24B-ZPDSS
J2, J3, J4, J5: Conn_01x06; SM06B-PASS
J6: Conn_01x03; SM03B-PASS
L221: 15u; L_Changjiang_FNR5040S
R6: 68k; R_0402_1005Metric
R7: 10k; R_0402_1005Metric
U2: MP2459GJ-Z-MS; TSOT-23-6

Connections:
+3V3: J1.4, J2.2, J3.2, J4.2, J5.2
+6V: C1.1, C12.1, D1.2 (A), J6.2, L221.1, R6.1
/BST: C8.1, U2.1 (BST)
/CLK: J1.8, J2.5, J3.5, J4.5, J5.5
/CS0: J1.1, J4.6
/CS1: J1.2, J3.6
/CS2: J1.5, J5.6
/CS3: J1.6, J2.6
/FB: C12.2, R6.2, R7.1, U2.3 (FB)
/MISO: J1.11, J2.3, J3.3, J4.3, J5.3
/MOSI: J1.12, J2.4, J3.4, J4.4, J5.4
/PWM: J1.7, J6.3
/SW: C8.2, D2.1 (K), L221.2, U2.6 (SW)
GND: C1.2, C7.2, D2.2 (A), J1.3, J1.15, J2.1, J3.1, J4.1, J5.1, J6.1, R7.2, U2.2 (GND)
VBUS: C7.1, D1.1 (K), J1.16, U2.4 (EN), U2.5 (IN)


Board: 2 copper layers, 45.0 x 36.0 mm, 18 parts (0 on the bottom side), 15 nets.

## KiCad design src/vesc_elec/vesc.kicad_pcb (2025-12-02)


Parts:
C1: 33n; C_0402_1005Metric
C8: 2u2; C_0603_1608Metric
D3: RED; LED_0603_1608Metric
D4: GRN; LED_0603_1608Metric
D5: BLU; LED_0603_1608Metric
D102: 5V; SOT-523
D105: 3V3; Diodes_UDFN-10_1.0x2.5mm_P0.5mm
D210: 30V; D_SMF
H1, H2, H8, H13: MountingHole; M2.5
J1: Conn_01x02; SM02B-PASS
J2: Conn_01x03; MR60-F-TopMount
J3: Conn_01x02; XT30PW-M_1x02_P2.50mm_Top_mount
J**1: USB_C_Receptacle_USB2.0_14P
P4: HALL/Encoder; SM06B-PASS
R1: 220k; R_0402_1005Metric
R2: 10k; R_0402_1005Metric
R3, R4: 22R; R_0402_1005Metric
R10, R11: 470R; R_0402_1005Metric
R12: 2k2; R_0402_1005Metric

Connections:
/CAN bus transceiver/CANH: J1.2; also elsewhere on the board
/CAN bus transceiver/CANL: J1.1; also elsewhere on the board
/Filters/HALL1_IN: D105.4, D105.7, P4.4; also elsewhere on the board
/Filters/HALL2_IN: D105.2, D105.9, P4.5; also elsewhere on the board
/Filters/TEMP_IN: D105.5, D105.6, P4.3; also elsewhere on the board
/HALL3: D105.1, D105.10, P4.6; also elsewhere on the board
/MCU/AN_IN: C1.2, R1.2, R2.2; also elsewhere on the board
/MCU/LED_GREEN: R11.2; also elsewhere on the board
/MCU/LED_RED: R10.2; also elsewhere on the board
/MCU/USB_D+: R4.1; also elsewhere on the board
/MCU/USB_D-: R3.1; also elsewhere on the board
/Mosfet driver/H1_VS: J2.3; also elsewhere on the board
/Mosfet driver/H2_VS: J2.2; also elsewhere on the board
/Mosfet driver/H3_VS: J2.1; also elsewhere on the board
GND: C1.1, C8.2, D3.1 (K), D4.1 (K), D5.1 (K), D102.3, D105.3, D105.8, D210.2 (A2), J3.1, J**1.A1 (GND), J**1.B1 (GND), J**1.SH (Shield), P4.1, R2.1; also elsewhere on the board
unnamed: D3.2 (A), R10.1
unnamed: D4.2 (A), R11.1
unnamed: D5.2 (A), R12.1
unnamed: D102.1, J**1.A7 (DN1), J**1.B7 (DN2), R3.2
unnamed: D102.2, J**1.A6 (DP1), J**1.B6 (DP2), R4.2
VCC: C8.1, P4.2, R12.2; also elsewhere on the board
V_SUPPLY: D210.1 (A1), J3.2, R1.1; also elsewhere on the board

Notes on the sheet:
Power Pads
Mounting Holes
Cheap F Cer 2
Change resistance value in code for voltage divider
Voltage supply (0 - 51v)


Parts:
C12, C14: 10n; C_0402_1005Metric
C13: 100p; C_0402_1005Metric
C15, C31: 4u7; C_1210_3225Metric
C16, C29, C33, C34, C57, C58: 1n; C_0402_1005Metric
C17: 100n; C_0603_1608Metric
C18, C24, C27: 330n; C_0603_1608Metric
C19: 22u; C_1210_3225Metric
C23: 33n; C_0603_1608Metric
C26: 4u7; C_1206_3216Metric
C28, C30: 2u2; C_0603_1608Metric
C32: 220n; C_0402_1005Metric
C59: 100n; C_0402_1005Metric
D601: D_Schottky; D_SOD-123
L1: 47u; L_Changjiang_FXL0630
R6, R22, R23, R34, R35, R69, R70, R73: 10k; R_0402_1005Metric
R8, R20: 15k; R_0402_1005Metric
R18: 4k7; R_0402_1005Metric
R19: 220k; R_0402_1005Metric
R24, R26, R28, R30, R66, R67: 1k; R_0402_1005Metric
R25, R29, R32, R38: 2k2; R_0402_1005Metric
R27, R31, R36: 47k; R_0402_1005Metric
U2: DRV8301; HTSSOP-56_6.1x14-0.5-EP
U4: TP2604-SR; SOP-8_3.76x4.96mm_P1.27mm

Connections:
/MCU/BR_SO1: C16.2, R26.1; also elsewhere on the board
/MCU/BR_SO2: C57.2, R28.1; also elsewhere on the board
/MCU/BR_SO3: C58.2, R30.1; also elsewhere on the board
/MCU/CS: U2.8 (nSCS); also elsewhere on the board
/MCU/EN_GATE: R25.1, U2.16 (EN_GATE); also elsewhere on the board
/MCU/FAULT: R22.2, U2.6 (FAULT); also elsewhere on the board
/MCU/H1: U2.17 (INH_A); also elsewhere on the board
/MCU/H2: U2.19 (INH_B); also elsewhere on the board
/MCU/H3: U2.21 (INH_C); also elsewhere on the board
/MCU/L1: U2.18 (INL_A); also elsewhere on the board
/MCU/L2: U2.20 (INL_B); also elsewhere on the board
/MCU/L3: U2.22 (INL_C); also elsewhere on the board
/MCU/SDI: U2.9 (SDI); also elsewhere on the board
/MCU/SDO: R24.1, U2.10 (SDO); also elsewhere on the board
/MCU/SENS1: R27.2, R29.2; also elsewhere on the board
/MCU/SENS2: R31.2, R32.2; also elsewhere on the board
/MCU/SENS3: R36.2, R38.2; also elsewhere on the board
/MCU/SLCK: U2.11 (SCLK); also elsewhere on the board
/Mosfet driver/GH_A: U2.47 (GH_A); also elsewhere on the board
/Mosfet driver/GH_B: U2.42 (GH_B); also elsewhere on the board
/Mosfet driver/GH_C: U2.37 (GH_C); also elsewhere on the board
/Mosfet driver/GL_A: U2.45 (GL_A); also elsewhere on the board
/Mosfet driver/GL_B: U2.40 (GL_B); also elsewhere on the board
/Mosfet driver/GL_C: U2.35 (GL_C); also elsewhere on the board
/Mosfet driver/H1_VS: C27.2, R27.1, U2.46 (SH_A); also elsewhere on the board
/Mosfet driver/H2_VS: C24.2, R31.1, U2.41 (SH_B); also elsewhere on the board
/Mosfet driver/H3_VS: C18.2, R36.1, U2.36 (SH_C); also elsewhere on the board
GND: C12.1, C13.1, C14.2, C15.1, C16.1, C19.1, C26.2, C28.2, C29.1, C30.1, C31.1, C32.1, C33.2, C34.2, C57.1, C58.1, C59.2, D601.2 (A), R18.2, R19.2, R23.1, R29.1, R32.1, R35.2, R38.1, R67.2, U2.28 (AVGND), U2.30 (SP2), U2.32 (SP1), U2.57 (GND), U4.4 (V-); also elsewhere on the board
unnamed: C12.2, R20.2
unnamed: C17.2, D601.1 (K), L1.1, U2.50 (PH), U2.51 (PH)
unnamed: R6.2, R69.1
unnamed: R6.1, R30.2, U4.1
unnamed: R70.2, R73.1
unnamed: C30.2, U2.27 (AVDD)
unnamed: C27.1, U2.48 (BST_A)
unnamed: C24.1, U2.43 (BST_B)
unnamed: C17.1, U2.52 (BST_BK)
unnamed: C18.1, U2.38 (BST_C)
unnamed: C13.2, R20.1, U2.2 (COMP)
unnamed: C23.2, U2.14 (CP1)
unnamed: C23.1, U2.15 (CP2)
unnamed: R23.2, U2.7 (DTC)
unnamed: C28.1, U2.23 (DVDD)
unnamed: C26.1, U2.13 (GVDD)
unnamed: R19.1, U2.1 (RT_CLK)
unnamed: R26.2, U2.25 (S01)
unnamed: R28.2, U2.26 (S02)
unnamed: C14.1, U2.56 (SS_TR)
unnamed: R8.2, R18.1, U2.3 (VSENSE)
unnamed: R67.1, R73.2, U4.3 (+)
unnamed: R66.1, R69.2, U4.2 (-)
unnamed: C59.1, R34.2, R35.1, U4.5 (+)
unnamed: R70.1, U4.6 (-), U4.7
SNA: C29.2, U2.33 (SN2), U2.44 (SL_A); also elsewhere on the board
SNB: C33.1, U2.31 (SN2), U2.39 (SL_B); also elsewhere on the board
SNC: C34.1, R66.2, U2.34 (SL_C); also elsewhere on the board
VCC: C19.2, C32.2, L1.2, R8.1, R22.1, R24.2, R25.2, R34.1, U2.24 (REF), U2.49 (VDD_SPI), U4.8 (V+); also elsewhere on the board
V_SUPPLY: C15.2, C31.2, U2.29 (PVDD1), U2.53 (PVDD2), U2.54 (PVDD2); also elsewhere on the board

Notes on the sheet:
C15 and C31 must be 50V rated. C18, C24 and C27 must be 25V rated.
Phase 1 and 3 switched on MOSFET side: - Driver BST,GH,SH,GL,SL - Phase sense voltage dividers - SNC to driver amp and SNA to external amp
Op Amp Current Sense for 3rd Phase
Change resistances used in code for voltage dividers
Phase sense voltage dividers


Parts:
C9, C46, C47, C48, C49, C53: 220n; C_0402_1005Metric
C45: 4u7; C_0805_2012Metric
C50, C51: 10p; C_0402_1005Metric
C52: 100n; C_0402_1005Metric
C55, C56: 2u2; C_0603_1608Metric
D501: 3V3; Diodes_UDFN-10_1.0x2.5mm_P0.5mm
J7: Conn_02x03_Odd_Even; IDC6
R5: 470R; R_0402_1005Metric
R501: 10k; R_0402_1005Metric
U5: STM32F405RGT6; LQFP-64-0.5
Y1: Crystal_GND24_Small; Crystal_SMD_2016-4Pin_2.0x1.6mm

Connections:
/CAN bus transceiver/CAN_RX: U5.61 (PB8); also elsewhere on the board
/CAN bus transceiver/CAN_TX: U5.62 (PB9); also elsewhere on the board
/Filters/HALL1_IN: U5.37 (PC6); also elsewhere on the board
/Filters/HALL2_IN: U5.38 (PC7); also elsewhere on the board
/Filters/TEMP_IN: U5.24 (PC4(ADC12_IN14)); also elsewhere on the board
/HALL3: U5.39 (PC8); also elsewhere on the board
/MCU/ADC_TEMP: U5.17 (PA3(ADC123_IN3)); also elsewhere on the board
/MCU/AN_IN: U5.11 (PC3(ADC123_IN13)); also elsewhere on the board
/MCU/BR_SO1: U5.8 (PC0(ADC123_IN10)); also elsewhere on the board
/MCU/BR_SO2: U5.9 (PC1(ADC123_IN11)); also elsewhere on the board
/MCU/BR_SO3: U5.10 (PC2(ADC123_IN12)); also elsewhere on the board
/MCU/CS: U5.40 (PC9); also elsewhere on the board
/MCU/EN_GATE: U5.57 (PB5); also elsewhere on the board
/MCU/FAULT: U5.59 (PB7); also elsewhere on the board
/MCU/H1: U5.41 (PA8); also elsewhere on the board
/MCU/H2: U5.42 (PA9(OTG_FS_VBUS)); also elsewhere on the board
/MCU/H3: U5.43 (PA10); also elsewhere on the board
/MCU/L1: U5.34 (PB13(OTG_HS_VBUS)); also elsewhere on the board
/MCU/L2: U5.35 (PB14); also elsewhere on the board
/MCU/L3: U5.36 (PB15); also elsewhere on the board
/MCU/LED_GREEN: U5.26 (PB0(ADC12_IN8)); also elsewhere on the board
/MCU/LED_RED: U5.27 (PB1(ADC12_IN9)); also elsewhere on the board
/MCU/NRST: C52.2, D501.4, D501.7, J7.2, U5.7 (NRST)
/MCU/SDI: U5.53 (PC12); also elsewhere on the board
/MCU/SDO: U5.52 (PC11); also elsewhere on the board
/MCU/SENS1: U5.14 (PA0(ADC123_IN0/WKUP)); also elsewhere on the board
/MCU/SENS2: U5.15 (PA1(ADC123_IN1)); also elsewhere on the board
/MCU/SENS3: U5.16 (PA2(ADC123_IN2)); also elsewhere on the board
/MCU/SLCK: U5.51 (PC10); also elsewhere on the board
/MCU/SWCLK: D501.2, D501.9, J7.6, R501.1, U5.49 (PA14(JTCK-SWCLK))
/MCU/SWDIO: D501.1, D501.10, J7.5, U5.46 (PA13(JTMS-SWDIO))
/MCU/SWO_UART: D501.5, D501.6, J7.1, U5.55 (PB3(JTDO/TRACESWO))
/MCU/USB_D+: U5.45 (PA12); also elsewhere on the board
/MCU/USB_D-: U5.44 (PA11); also elsewhere on the board
GND: C9.1, C45.1, C46.1, C47.1, C48.1, C49.1, C50.2, C51.2, C52.1, C53.1, C55.2, C56.2, D501.3, D501.8, J7.3, U5.12 (VSSA), U5.18 (VSS), U5.60 (BOOT0(VPP)), U5.63 (VSS), Y1.2, Y1.4; also elsewhere on the board
unnamed: C50.1, R5.2, Y1.1
unnamed: R5.1, U5.5 (PH0-OSC_IN)
unnamed: C51.1, U5.6 (PH1-OSC_OUT), Y1.3
unnamed: C55.1, U5.31 (VCAP1)
unnamed: C56.1, U5.47 (VCAP2)
VCC: C9.2, C45.2, C46.2, C47.2, C48.2, C49.2, C53.2, J7.4, R501.2, U5.1 (VBAT), U5.13 (VDDA), U5.19 (VDD), U5.32 (VDD), U5.48 (VDD), U5.64 (VDD); also elsewhere on the board

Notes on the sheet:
Reset pin internally pulled up
Required for USB to work
Programming / Debug connector
Bypass, place next to VDD pins


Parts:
C35, C36, C37: 4u7; C_1210_3225Metric
C38, C39: 270u; CP_Elec_10x10
C40, C41, C42: 3n3; C_0402_1005Metric
C61, C62, C63, C65, C66, C67: 1n; C_0402_1005Metric
Q1, Q2, Q3, Q4, Q5, Q6: NCEP60T20; TO-220-3-heatsink-pad-tabdown
R33, R37, R39, R41, R42, R43, R47, R48, R49, R53, R54, R55: 10R; R_0402_1005Metric
R44, R45, R46, R50, R51, R52: 4k7; R_0402_1005Metric
R56, R57, R58, R59, R60, R61: 1m; R_2512_6332Metric

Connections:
/Mosfet driver/GH_A: R43.2; also elsewhere on the board
/Mosfet driver/GH_B: R42.2; also elsewhere on the board
/Mosfet driver/GH_C: R41.2; also elsewhere on the board
/Mosfet driver/GL_A: R49.2; also elsewhere on the board
/Mosfet driver/GL_B: R48.2; also elsewhere on the board
/Mosfet driver/GL_C: R47.2; also elsewhere on the board
/Mosfet driver/H1_VS: C42.1, C66.2, Q3.3 (S), Q6.2 (D), Q6.4 (Heatsink), R46.1; also elsewhere on the board
/Mosfet driver/H2_VS: C41.1, C63.2, Q2.3 (S), Q5.2 (D), Q5.4 (Heatsink), R45.1; also elsewhere on the board
/Mosfet driver/H3_VS: C40.1, C61.2, Q1.3 (S), Q4.2 (D), Q4.4 (Heatsink), R44.2; also elsewhere on the board
GND: C35.1, C36.1, C37.1, C38.2, C39.2, R33.1, R37.1, R39.1, R53.1, R54.1, R55.1, R56.1, R57.1, R58.1, R59.1, R60.1, R61.1; also elsewhere on the board
unnamed: C40.2, R33.2, R53.2
unnamed: C41.2, R37.2, R54.2
unnamed: C42.2, R39.2, R55.2
unnamed: C61.1, Q1.1 (G), R41.1, R44.1
unnamed: C63.1, Q2.1 (G), R42.1, R45.2
unnamed: C66.1, Q3.1 (G), R43.1, R46.2
unnamed: C62.1, Q4.1 (G), R47.1, R50.1
unnamed: C65.1, Q5.1 (G), R48.1, R51.2
unnamed: C67.1, Q6.1 (G), R49.1, R52.2
SNA: C67.2, Q6.3 (S), R52.1, R60.2, R61.2; also elsewhere on the board
SNB: C65.2, Q5.3 (S), R51.1, R58.2, R59.2; also elsewhere on the board
SNC: C62.2, Q4.3 (S), R50.2, R56.2, R57.2; also elsewhere on the board
V_SUPPLY: C35.2, C36.2, C37.2, C38.1, C39.1, Q1.2 (D), Q1.4 (Heatsink), Q2.2 (D), Q2.4 (Heatsink), Q3.2 (D), Q3.4 (Heatsink); also elsewhere on the board

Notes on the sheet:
Choice of MOSFET is important. 60V mininmum Vds and 2.5ohm max Rds(on) are strongly advised. The lower the Rds(on), the less energy is wasted to heat dissipation.
C35, C36 and C37 must be 50V rated and placed close to each stage.
Choice of electrolytic capcitors is important. 10,000 hour lifetime, low-ESR, low-impedance, and high ripple current ratings are strongly advised.


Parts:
C6: 100n; C_0402_1005Metric
R14: 10k; R_0402_1005Metric
R15, R16, R17: 2k2; R_0402_1005Metric

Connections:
/Filters/HALL1_IN: R17.1; also elsewhere on the board
/Filters/HALL2_IN: R16.1; also elsewhere on the board
/Filters/TEMP_IN: C6.2, R14.1; also elsewhere on the board
/HALL3: R15.1; also elsewhere on the board
GND: C6.1; also elsewhere on the board
VCC: R14.2, R15.2, R16.2, R17.2; also elsewhere on the board


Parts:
C5: 2u2; C_0603_1608Metric
R13: 10k; R_0402_1005Metric
TH401: 10k; R_0402_1005Metric

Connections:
/MCU/ADC_TEMP: C5.1, R13.1, TH401.2; also elsewhere on the board
GND: C5.2, R13.2; also elsewhere on the board
VCC: TH401.1; also elsewhere on the board


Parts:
C2: 2u2; C_0603_1608Metric
C3, C7: 10u; C_1206_3216Metric
C4, C201: 220n; C_0402_1005Metric
D101: 5V; SOT-523
U1: HX4002; SOT-23-6
U3: TCAN1462V; SOIC-8_3.9x4.9mm_P1.27mm

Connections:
/CAN bus transceiver/CANH: D101.1, U3.7 (CANH); also elsewhere on the board
/CAN bus transceiver/CANL: D101.2, U3.6 (CANL); also elsewhere on the board
/CAN bus transceiver/CAN_RX: U3.4 (RXD); also elsewhere on the board
/CAN bus transceiver/CAN_TX: U3.1 (TXD); also elsewhere on the board
GND: C3.2, C4.2, C7.2, C201.2, D101.3, U1.2 (GND), U3.2 (GND), U3.8 (STB), U3.9 (EP); also elsewhere on the board
unnamed: C2.1, U1.6 (CP+)
unnamed: C2.2, U1.4 (CP-)
unnamed: C4.1, C7.1, U1.1 (VOUT), U3.3 (VCC)
VCC: C3.1, C201.1, U1.3 (~SHDN), U1.5 (VIN), U3.5 (VIO); also elsewhere on the board

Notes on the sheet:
STB tied to GND - normal mode only



Board: 6 copper layers, 80.0 x 95.0 mm, 153 parts (135 on the bottom side), 98 nets.

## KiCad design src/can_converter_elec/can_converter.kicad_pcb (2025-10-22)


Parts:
D1: XL-1608UYC-06; LED_0603_1608Metric; MPN KPT-1608SGC
D2: XL-1608UGC-04; LED_0603_1608Metric; MPN KPT-1608SGC
D3: XL-1608SURC-06; LED_0603_1608Metric; MPN KPT-1608EC
H1, H2: MountingHole; M2.5
J1: SM02B-PASS
R1, R2: 4K7; R_0402_1005Metric; MPN any
R3, R4, R5: 1K; R_0402_1005Metric; MPN any
X1: 629722000214_pasteInHole; USB_C_Receptacle_USB2.0_14P; MPN 629722000214

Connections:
+3V3: R3.1, R4.1, R5.1; also elsewhere on the board
+5V: X1.A4 (VBUS), X1.B4 (VBUS); also elsewhere on the board
/CAN Transceiver/CAN1_H: J1.2; also elsewhere on the board
/CAN Transceiver/CAN1_L: J1.1; also elsewhere on the board
/MCU/LED_RX: D2.2 (K); also elsewhere on the board
/MCU/LED_TX: D1.2 (K); also elsewhere on the board
/USB_N: X1.A7 (DN1), X1.B7 (DN2); also elsewhere on the board
/USB_P: X1.A6 (DP1), X1.B6 (DP2); also elsewhere on the board
GND: D3.2 (K), R1.2, R2.2, X1.A1 (GND), X1.B1 (GND), X1.SH (Shield); also elsewhere on the board
unnamed: D1.1 (A), R3.2
unnamed: D2.1 (A), R4.2
unnamed: D3.1 (A), R5.2
unnamed: R2.1, X1.A5 (CC1)
unnamed: R1.1, X1.B5 (CC2)


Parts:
C6, C7: 10u; C_1206_3216Metric; MPN any
PS1: RT9013-33GB; SOT-23-5; Mouser Part Number 835-RT9013-33GB

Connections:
+3V3: C7.1, PS1.5 (VOUT); also elsewhere on the board
+5V: C6.1, PS1.1 (VIN), PS1.3 (EN); also elsewhere on the board
GND: C6.2, C7.2, PS1.2 (GND); also elsewhere on the board

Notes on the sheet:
Power: - MCU: 13mA (64MHz, DBG, FDCAN1/2, GPIO[A..D], TIM1, USB) - LEDs: 2x 1mA ?? - CAN: 2x ??


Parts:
C8, C9: 220n; C_0402_1005Metric; MPN any
U2: TCAN1462V; SOIC-8_3.9x4.9mm_P1.27mm

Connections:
+3V3: C8.1, U2.5 (VIO); also elsewhere on the board
+5V: C9.1, U2.3 (VCC); also elsewhere on the board
/CAN Transceiver/CAN1_H: U2.7 (CANH); also elsewhere on the board
/CAN Transceiver/CAN1_L: U2.6 (CANL); also elsewhere on the board
/CAN Transceiver/CAN1_RX: U2.4 (RXD); also elsewhere on the board
/CAN Transceiver/CAN1_S: U2.8 (STB); also elsewhere on the board
/CAN Transceiver/CAN1_TX: U2.1 (TXD); also elsewhere on the board
GND: C8.2, C9.2, U2.2 (GND), U2.9 (EP); also elsewhere on the board


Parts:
C1, C2: 10p; C_0402_1005Metric; MPN any
C3: 10n; C_0402_1005Metric; MPN MC0603B104K500CT
C4: 220n; C_0402_1005Metric; MPN MC0603B104K500CT
R7, R8: 100k; R_0402_1005Metric
R9: 470R; R_0402_1005Metric
U1: STM32G0B1CBT; LQFP-48_7x7mm_P0.5mm; MPN STM32G0B1CBT
Y1: 830108313809; Crystal_SMD_2016-4Pin_2.0x1.6mm; MPN 830108313809

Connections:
+3V3: C4.1, R7.2, U1.4 (VBAT), U1.5 (VREF+), U1.6 (VDD/VDDA); also elsewhere on the board
/CAN Transceiver/CAN1_RX: U1.38 (PD0); also elsewhere on the board
/CAN Transceiver/CAN1_S: U1.37 (PA15); also elsewhere on the board
/CAN Transceiver/CAN1_TX: U1.39 (PD1); also elsewhere on the board
/MCU/LED_RX: U1.14 (PA3); also elsewhere on the board
/MCU/LED_TX: U1.15 (PA4); also elsewhere on the board
/MCU/NRST: C3.1, U1.10 (PF2/NRST)
/MCU/SWCLK: R8.2, U1.36 (PA14/BOOT0)
/MCU/SWDIO: R7.1, U1.35 (PA13)
/USB_N: U1.33 (PA11[PA9]); also elsewhere on the board
/USB_P: U1.34 (PA12[PA10]); also elsewhere on the board
GND: C1.1, C2.1, C3.2, C4.2, R8.1, U1.7 (VSS/VSSA), Y1.2 (GND), Y1.4 (GND); also elsewhere on the board
unnamed: C1.2, U1.8 (PF0/OSC_IN), Y1.3 (C_{2})
unnamed: R9.2, U1.9 (PF1/OSC_OUT)
unnamed: C2.2, R9.1, Y1.1 (C_{1})

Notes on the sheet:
NRST has a internal pullup ~40kΩ (see: DS13560 5.3.15 NRST input characteristics)
Load Caps C_{L} = ( (C_{1} C_{2}) / (C_{1} + C_{2}) ) + C_{Stray} 12pF -> 2x 6pF Caps Thay might not be needed


Board: 2 copper layers, 40.6 x 17.2 mm, 28 parts (1 on the bottom side), 23 nets.

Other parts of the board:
G**: LOGO; Monkey

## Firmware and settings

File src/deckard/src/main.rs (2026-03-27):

//! REPL for controlling the rover drivebase.
//!
//! Usage: `deckard [SocketCAN interface name] [Node ID]`
//!
//! # Testing
//!
//! ## Create a virtual CAN device
//!
//! ```
//! sudo modprobe vcan
//! sudo ip link add dev vcan0 type vcan
//! sudo ip link set up vcan0
//! ```
//!
//! ## Start the node
//!
//! ```
//! basic_node vcan0 [node ID]
//! ```
//!
//! ## Interact with the node using Yakut
//!
//! To subscribe and print out Heartbeat messages:
//! `yakut --transport "CAN(can.media.socketcan.SocketCANMedia('vcan0',8),42)" subscribe uavcan.node.Heartbeat.1.0`
//!
//! To send a NodeInfo request:
//! `yakut --transport "CAN(can.media.socketcan.SocketCANMedia('vcan0',8),42)" call [Node ID of basic_node] uavcan.node.GetInfo.1.0 {}`
//!
//! In the above two commands, 8 is the MTU of standard CAN and 42 is the node ID of the Yakut node.

extern crate canadensis;
extern crate canadensis_can;
extern crate canadensis_linux;
extern crate rand;
extern crate simplelog;
extern crate socketcan;

use std::convert::TryFrom;
use std::{env, time};
use std::time::Duration;
use std::io::{self, Write, ErrorKind};
use std::thread;
use std::collections::HashMap;
use std::sync::mpsc;
use std::process;

use half;
use ctrlc;
use socketcan::{CanFdSocket, CanSocket, Socket};

use canadensis::core::time::MicrosecondDuration32;
use canadensis::core::transfer::{MessageTransfer, ServiceTransfer};
use canadensis::core::transport::Transport;
use canadensis::core::{SubjectId, Priority};
use canadensis::node::{BasicNode, CoreNode};
use canadensis::requester::TransferIdFixedMap;
use canadensis::{Node, ResponseToken, TransferHandler};
use canadensis_can::queue::{ArrayQueue, SingleQueueDriver};
use canadensis_can::{CanNodeId, CanReceiver, CanTransmitter, CanTransport, Error, Mtu};
use canadensis::encoding::Deserialize;
use canadensis_data_types::uavcan::node::get_info_1_0::GetInfoResponse;
use canadensis_data_types::uavcan::node::version_1_0::Version;
use canadensis_data_types::reg::udral::service::actuator::common::sp::scalar_0_1::Scalar as VESCScalar;
use canadensis_data_types::reg::udral::physics::dynamics::rotation::planar_0_1::Planar as StepperPlanar;
use canadensis_data_types::reg::udral::physics::kinematics::rotation::planar_0_1::Planar;
use canadensis_data_types::uavcan::si::unit::angle::scalar_1_0 as angle_pos_scalar;
use canadensis_data_types::uavcan::si::unit::angular_velocity::scalar_1_0::Scalar as AVScalar;
use canadensis_data_types::uavcan::si::unit::angular_acceleration::scalar_1_0::Scalar as AAScalar;
use canadensis_data_types::uavcan::si::unit::torque::scalar_1_0::Scalar as TScalar;

use canadensis_linux::{LinuxCan, SystemClock};

mod cmd;
mod core;

// of the VESCs
// canonical ordering: FL, FR, BL, BR
const VESC_IDS: [u8; 4] = [10, 11, 12, 13];
const STEPPER_SETPOINT_SUB: [u16; 4] = [3000, 3010, 3020, 3030];
const STEPPER_POSITION_SUB: [u16; 4] = [3001, 3011, 3021, 3031];
const VESC_SPEED_SUB: [u16; 4] = [3050, 3060, 3070, 3080];

fn main() -> Result<(), Box<dyn std::error::Error>> {
    simplelog::TermLogger::init(
        simplelog::LevelFilter::Warn,
        simplelog::Config::default(),
        simplelog::TerminalMode::Stderr,
        simplelog::ColorChoice::Auto,
    )
    .unwrap();

    let mut args = env::args().skip(1);
    let stepper_can_interface = args.next().expect("Expected CAN interface name");
    let vesc_can_interface = args.next().expect("Expected CAN interface name");
    let node_id = CanNodeId::try_from(
        args.next()
            .expect("Expected node ID")
            .parse::<u8>()
            .expect("Invalid node ID format"),
    )
    .expect("Node ID too large");

    println!(
        "Port list size: {} bytes",
        std::mem::size_of::<canadensis_data_types::uavcan::node::port::list_1_0::List>()
    );

    let stepper_can = CanFdSocket::open(&stepper_can_interface).expect("Failed to open CAN interface");
    stepper_can.set_read_timeout(Duration::from_millis(100))?;
    stepper_can.set_write_timeout(Duration::from_millis(100))?;
    let stepper_can = LinuxCan::new(stepper_can);

    let vesc_can = CanSocket::open(&vesc_can_interface).expect("Failed to open CAN interface");
    vesc_can.set_read_timeout(Duration::from_millis(100))?;
    vesc_can.set_write_timeout(Duration::from_millis(100))?;
    let vesc_can = LinuxCan::new(vesc_can);

    let stepper_node_info = GetInfoResponse {
        protocol_version: Version { major: 1, minor: 0 },
        hardware_version: Version { major: 0, minor: 0 },
        software_version: Version { major: 0, minor: 1 },
        software_vcs_revision_id: 0,
        unique_id: rand::random(),
        name: heapless::Vec::from_slice(b"org.bluesat.obc.all").unwrap(),
        software_image_crc: heapless::Vec::new(),
        certificate_of_authenticity: Default::default(),
    };
    let vesc_node_info = GetInfoResponse {
        protocol_version: Version { major: 1, minor: 0 },
        hardware_version: Version { major: 0, minor: 0 },
        software_version: Version { major: 0, minor: 1 },
        software_vcs_revision_id: 0,
        unique_id: rand::random(),
        name: heapless::Vec::from_slice(b"org.bluesat.obc.vesc").unwrap(),
        software_image_crc: heapless::Vec::new(),
        certificate_of_authenticity: Default::default(),
    };

    const QUEUE_CAPACITY: usize = 1210;
    type FDQueue = SingleQueueDriver<SystemClock, ArrayQueue<QUEUE_CAPACITY>, LinuxCan<CanFdSocket>>;
    type ClassicQueue = SingleQueueDriver<SystemClock, ArrayQueue<QUEUE_CAPACITY>, LinuxCan<CanSocket>>;
    let stepper_queue_driver: FDQueue = SingleQueueDriver::new(ArrayQueue::new(), stepper_can);
    let vesc_queue_driver: ClassicQueue = SingleQueueDriver::new(ArrayQueue::new(), vesc_can);

    const TRANSFER_IDS: usize = 16;
    const PUBLISHERS: usize = 16;
    const REQUESTERS: usize = 16;

    let transmitter = CanTransmitter::new(Mtu::CanFd64);
    let receiver = CanReceiver::new(node_id);
    let stepper_core_node: CoreNode<
        SystemClock,
        CanTransmitter<SystemClock, FDQueue>,
        CanReceiver<SystemClock, FDQueue>,
        TransferIdFixedMap<CanTransport, TRANSFER_IDS>,
        FDQueue,
        PUBLISHERS,
        REQUESTERS,
    > = CoreNode::new(
        SystemClock::new(),
        node_id,
        transmitter,
        receiver,
        stepper_queue_driver,
    );
    let mut stepper_node = BasicNode::new(stepper_core_node, stepper_node_info).unwrap();

    let transmitter = CanTransmitter::new(Mtu::Can8);
    let receiver = CanReceiver::new(node_id);
    let vesc_core_node: CoreNode<
        SystemClock,
        CanTransmitter<SystemClock, ClassicQueue>,
        CanReceiver<SystemClock, ClassicQueue>,
        TransferIdFixedMap<CanTransport, TRANSFER_IDS>,
        ClassicQueue,
        PUBLISHERS,
        REQUESTERS,
    > = CoreNode::new(
        SystemClock::new(),
        node_id,
        transmitter,
        receiver,
        vesc_queue_driver,
    );
    let mut vesc_node = BasicNode::new(vesc_core_node, vesc_node_info).unwrap();

    let (cmd_tx, cmd_rx) = mpsc::channel::<core::NodeCommand>();
    let (notif_tx, notif_rx) = mpsc::channel::<Result<(),()>>();

    for subject in VESC_SPEED_SUB {
        println!("Publishing on {}...", subject);
        vesc_node.start_publishing(
            SubjectId::from_truncating(subject),
            MicrosecondDuration32::millis(1_000),
            Priority::Nominal
        ).unwrap();
    }
    for subject in STEPPER_SETPOINT_SUB {
        println!("Publishing on {}...", subject);
        stepper_node.start_publishing(
            SubjectId::from_truncating(subject),
            MicrosecondDuration32::millis(1_000),
            Priority::Nominal
        ).unwrap();
    }
    /*for subject in STEPPER_POSITION_SUB {
        println!("Subscribing to {}...", subject);
        stepper_node.subscribe_message(
            SubjectId::from_truncating(subject),
            size_of::<angle_pos_scalar::Scalar>(),
            MicrosecondDuration32::millis(1_000)
        ).unwrap();
    }*/

    let start_time = std::time::Instant::now();
    let mut prev_seconds = 0;
    let mut notify_in_flight = false;
    let mut notif_op_time = std::time::Instant::now();
    let mut rover_internal = RoverInternal::new();
    // core thread
    // needs to handle node.receive and node.run_per_second_tasks
    // also handles other operations on the node via message passing from the REPL thread
    thread::spawn(move || loop {
        // node handler loop
        match vesc_node.receive(&mut rover_internal) {
        // TODO: more brain cells needed here
            Ok(_) => {}
            Err(Error::Driver(e)) if e.kind() == ErrorKind::WouldBlock => {},
            Err(e) => panic!("{:?}", e),
        }
        match stepper_node.receive(&mut rover_internal) {
            Ok(_) => {},
            Err(Error::Driver(e)) if e.kind() == ErrorKind::WouldBlock => {},
            Err(e) => panic!("{:?}", e),
        }
        match cmd_rx.try_recv() {
            Ok(msg) => {
                match msg.op {
                    core::Operation::DriveStepper => {
                        rover_internal.target_stepper_pos = msg.values;
                        // send the message thrice for redundancy
                        for _ in 0..3 {
                            for i in 0..4 {
                                let payload = StepperPlanar {
                                    kinematics: Planar {
                                        angular_position: angle_pos_scalar::Scalar { radian: msg.values[i] },
                                        angular_velocity: AVScalar { radian_per_second: f32::NAN },
                                        angular_acceleration: AAScalar { radian_per_second_per_second: f32::NAN },
                                    },
                                    torque: TScalar {
                                        newton_meter: f32::NAN
                                    }
                                };
                                stepper_node.publish(STEPPER_SETPOINT_SUB[i].try_into().unwrap(), &payload).unwrap();
                            }
                            stepper_node.flush().unwrap();
                            thread::sleep(time::Duration::from_millis(19)); // arbitrary number (-:
                        }
                    }
                    core::Operation::DriveVesc => {
                        // send messages thrice for redundancy
                        for _ in 0..3 {
                            for i in 0..4 {
                                let payload = VESCScalar {
                                    value: half::f16::from_f32(msg.values[i])
                                };
                                vesc_node.publish(VESC_SPEED_SUB[i].try_into().unwrap(), &payload).unwrap();
                            }
                            vesc_node.flush().unwrap();
                            thread::sleep(time::Duration::from_millis(19));
                        }
                    }
                    // this operation only makes sense in the context of the stepper
                    // to avoid deadlock, caller must NEVER call this twice in succession;
                    // it must do a blocking recv on the first call before calling again
                    core::Operation::NotifyWhenDone => {
                        println!("[BACKEND] Blocking on steering finishing...");
                        notify_in_flight = true;
                        notif_op_time = std::time::Instant::now();
                    }
                }
            }
            Err(_) => {}
        }
        if notify_in_flight {
            /*if rover_internal.is_idle() {
                /*notif_tx.send(Ok(())).unwrap();
                notify_in_flight = false;
                println!("[BACKEND] Steering resolved (motors reporting idle)");*/
            } else */if std::time::Instant::now().duration_since(notif_op_time).as_secs() >= 3 {
                // 3-second timeout
                notif_tx.send(Ok(())).unwrap();
                notify_in_flight = false;
                println!("[BACKEND] Steering resolved (3-second timeout)");
            }
        }
        let seconds = std::time::Instant::now()
            .duration_since(start_time)
            .as_secs();
        if seconds != prev_seconds {
            prev_seconds = seconds;
            vesc_node.run_per_second_tasks().unwrap();
            vesc_node.flush().unwrap();
            stepper_node.run_per_second_tasks().unwrap();
            stepper_node.flush().unwrap();
        }
    });

    // assuming we start in this state...
    let mut rover = core::Rover {
        cmd_tx: cmd_tx.clone(),
        notif_rx,
        wheels: core::WheelOrientation::Aligned(0.0),
        is_stopped: true,
    };

    ctrlc::set_handler(move || {
        println!("\nStopping rover...");
        cmd_tx.send(core::NodeCommand {
            op: core::Operation::DriveVesc,
            values: [0.0; 4] // drive: position 0
        }).unwrap();
        thread::sleep(time::Duration::from_secs(1));
        process::exit(1);
    }).expect("Error setting ^C handler");

    let commands: [Box<dyn cmd::Cmd>; 4] = [
        Box::new(cmd::Move {}),
        Box::new(cmd::Stop {}),
        Box::new(cmd::Help {}),
        Box::new(cmd::Quit {}),
    ];
    let mut keyword_lookup = HashMap::new();
    for i in 0..commands.len() {
        let command = &commands[i];
        for keyword in command.get_keywords() {
            keyword_lookup.insert(keyword, i);
        }
    }
    println!("Welcome to the new and improved (?) drivebase controller.");
    println!("Type 'help' for a list of commands, and 'help <command>' for command-specific help.");
    let mut q_safety_interlock = true;
    loop {
        print!("> ");
        io::stdout().flush().unwrap();

        let mut input = String::new();
        match io::stdin().read_line(&mut input) {
            Err(_) => {
                eprintln!("Error reading input");
                continue;
            }
            Ok(b) => {
                if b == 0 {
                    // EOF
                    print!("\n");
                    break;
                }
            }
        }

        let input = input.trim();
        if input.is_empty() {
            continue;
        }

        let parts: Vec<&str> = input.split_whitespace().collect();
        let keyword = parts[0].to_lowercase();

        // special case: help command
        if keyword == "help" || keyword == "h" {
            if parts.len() < 2 {
                for command in commands.iter() {
                    println!("{}\t{}", command.get_keywords()[0], command.get_brief());
                }
                println!("Note commands and aliases are not case-sensitive.");
            } else {
                let help_keyword = parts[1].to_lowercase();
                if help_keyword == "help" || help_keyword == "h" {
                    println!("Usage: help\nOr:    help <command>");
                    println!("In the first form, lists available commands.");
                    println!("In the second form, provides more detailed information about a command.");
                }
                match keyword_lookup.get(help_keyword.as_str()) {
                    Some(cmd_idx) => {
                        let cmd = &commands[*cmd_idx];
                        println!("{}", cmd.get_help());
                    }
                    None => {
                        eprintln!("The word {} is not a recognised command or alias.", keyword);
                    }
                }
            }
        } else if keyword == "q" && q_safety_interlock {
            println!("NOTE: if you want to quit this program, use '!' instead.");
            println!("Rerun this command if you really do want to strafe left (move the rover).");
            println!("This message only appears once.");
            q_safety_interlock = false;
        } else if keyword == "!" || keyword == "quit" || keyword == "exit" {
            // second special case: quit
            if !rover.is_stopped {
                println!("WARNING! Rover is STILL MOVING!!!!");
                break;
            } else if rover.wheels != core::WheelOrientation::Aligned(0.0) {
                print!("Rover wheels aren't aligned. Do you want to exit anyway? (y/n) ");
                io::stdout().flush().unwrap();
                let mut input = String::new();
                match io::stdin().read_line(&mut input) {
                    Err(_) => {
                        eprintln!("Error reading input");
                        continue;
                    }
                    Ok(_) => {
                        let input = input.trim();
                        if input == "y" || input == "yes" {
                            break;
                        } else {
                            continue
                        }
                    }
                }
            } else {
                break;
            }
        } else {
            match keyword_lookup.get(keyword.as_str()) {
                Some(cmd_idx) => {
                    let cmd = &commands[*cmd_idx];
                    match cmd.run(parts, &mut rover) {
                        Ok(_) => println!("Ok."),
                        Err(_) => println!("Error executing command.")
                    }
                }
                None => {
                    eprintln!("The word {} is not a recognised command or alias.", keyword);
                    eprintln!("Type 'help' for a list of commands.");
                }
            }
        }
    }
    println!("Stopping rover...");
    rover.cmd_tx.send(core::NodeCommand {
        op: core::Operation::DriveVesc,
        values: [0.0; 4] // drive: position 0
    }).unwrap();
    thread::sleep(time::Duration::from_secs(1));
    Ok(())
}

struct RoverInternal {
    curr_stepper_pos: [f32; 4],
    target_stepper_pos: [f32; 4],
}

impl RoverInternal {
    fn new() -> Self {
        Self {
            curr_stepper_pos: [0.0; 4],
            target_stepper_pos: [0.0; 4],
        }
    }
    
    fn is_idle(&self) -> bool {
        let mut is_idle = true;
        for i in 0..4 {
            let delta = self.curr_stepper_pos[i] - self.target_stepper_pos[i];
            const EPSILON: f32 = 0.001;
            if f32::abs(delta) >= EPSILON {
                is_idle = false;
            }
            println!("stepper {} has delta {}", i, delta);
        }
        is_idle
    }
}

impl<T: Transport> TransferHandler<T> for RoverInternal {
    fn handle_message<N>(&mut self, _node: &mut N, transfer: &MessageTransfer<Vec<u8>, T>) -> bool
    where
        N: Node<Transport = T>,
    {
        let Some(idx) = STEPPER_POSITION_SUB.iter().position(|&r| r == u16::from(transfer.header.subject)) else {
            // TODO: handle more messages here from nodes (Heartbeat?) for diagnostics
            return false;
        };
        // we're handling a stepper position message
        println!("idx {} bytes {:?}", idx, transfer.payload);
        let Ok(stepper_pos) =
            angle_pos_scalar::Scalar::deserialize_from_bytes(&transfer.payload)
        else {
            return false;
        };
        self.curr_stepper_pos[idx] = stepper_pos.radian;
        true
    }

    fn handle_request<N>(
        &mut self,
        _node: &mut N,
        _token: ResponseToken<T>,
        transfer: &ServiceTransfer<Vec<u8>, T>,
    ) -> bool
    where
        N: Node<Transport = T>,
    {
        println!("Got request {:?}", transfer);
        false
    }

    fn handle_response<N>(&mut self, _node: &mut N, transfer: &ServiceTransfer<Vec<u8>, T>) -> bool
    where
        N: Node<Transport = T>,
    {
        println!("Got response {:?}", transfer);
        false
    }
}

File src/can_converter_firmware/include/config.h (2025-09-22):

/*

The MIT License (MIT)

Copyright (c) 2016 Hubert Denkmair

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
*
*
* Some board-specific defines here, such as :
* - USB strings
* - LED pin assignments and polarity
* - other special pins to control CAN transceivers.
*
* CAN_S_PIN: Some CAN transceivers (e.g. TJA1050) have a "Silent mode in which the transmitter is disabled";
* enabled with this 'S' pin. If undefined, the corresponding code will be disabled.
*
* TERM_Pin: Add support for an externally controlled terminating resistor
*
*/

#pragma once

#include "version.h"

#define CAN_QUEUE_SIZE				 (64 * NUM_CAN_CHANNEL)

#define USBD_VID					 0x1d50
#define USBD_PID_FS					 0x606f
#define USBD_LANGID_STRING			 1033
#define USBD_CONFIGURATION_STRING_FS GIT_HASH
#define USBD_INTERFACE_STRING_FS	 "gs_usb interface"

/*************** STM32F042 ***************/

#if defined(BOARD_canable)
	#define USBD_PRODUCT_STRING_FS	 "canable gs_usb"
	#define USBD_MANUFACTURER_STRING "canable.io"
	#define DFU_INTERFACE_STRING_FS	 "canable firmware upgrade interface"

	#define TIM2_CLOCK_SPEED		 48000000

	#define CAN_INTERFACE			 CAN
	#define CAN_CLOCK_SPEED			 48000000
	#define NUM_CAN_CHANNEL			 1

	#define LEDRX_GPIO_Port			 GPIOB
	#define LEDRX_Pin				 GPIO_PIN_0 /* green */
	#define LEDRX_Mode				 GPIO_MODE_OUTPUT_PP
	#define LEDRX_Active_High		 1

	#define LEDTX_GPIO_Port			 GPIOB
	#define LEDTX_Pin				 GPIO_PIN_1 /* blue */
	#define LEDTX_Mode				 GPIO_MODE_OUTPUT_PP
	#define LEDTX_Active_High		 0

#elif defined(BOARD_canalyze)
	#define USBD_PRODUCT_STRING_FS	 "CANAlyze gs_usb"
	#define USBD_MANUFACTURER_STRING "STMicroelectronics"
	#define DFU_INTERFACE_STRING_FS	 "CANAlyze firmware upgrade interface"

	#define TIM2_CLOCK_SPEED		 48000000

	#define CAN_INTERFACE			 CAN
	#define CAN_CLOCK_SPEED			 48000000
	#define NUM_CAN_CHANNEL			 1

	#define LEDRX_GPIO_Port			 GPIOB
	#define LEDRX_Pin				 GPIO_PIN_0 /* green */
	#define LEDRX_Mode				 GPIO_MODE_OUTPUT_PP
	#define LEDRX_Active_High		 1

	#define LEDTX_GPIO_Port			 GPIOB
	#define LEDTX_Pin				 GPIO_PIN_1 /* red */
	#define LEDTX_Mode				 GPIO_MODE_OUTPUT_PP
	#define LEDTX_Active_High		 1

#elif defined(BOARD_cannette)
	#define USBD_PRODUCT_STRING_FS	 "cannette gs_usb"
	#define USBD_MANUFACTURER_STRING "chacaltech"
	#define DFU_INTERFACE_STRING_FS	 "cannette firmware upgrade interface"

	#define TIM2_CLOCK_SPEED		 48000000

	#define CAN_INTERFACE			 CAN
	#define CAN_CLOCK_SPEED			 48000000
	#define NUM_CAN_CHANNEL			 1

	#define LEDRX_GPIO_Port			 GPIOA
	#define LEDRX_Pin				 GPIO_PIN_9 /* RX: green */
	#define LEDRX_Mode				 GPIO_MODE_OUTPUT_OD
	#define LEDRX_Active_High		 0

	#define LEDTX_GPIO_Port			 GPIOA
	#define LEDTX_Pin				 GPIO_PIN_8 /* TX: red */
	#define LEDTX_Mode				 GPIO_MODE_OUTPUT_OD
	#define LEDTX_Active_High		 0

	#define nCANSTBY_Port			 GPIOC
	#define nCANSTBY_Pin			 GPIO_PIN_14 /* control xceiver standby, active low */
	#define nCANSTBY_Active_High	 1

	#define nSI86EN_Port			 GPIOC
	#define nSI86EN_Pin				 GPIO_PIN_13 /* enable power to Si86xx isolater, active low */

	#define DCDCEN_Port				 GPIOC
	#define DCDCEN_Pin				 GPIO_PIN_15 /* activate DCDC converter, active high */

#elif defined(BOARD_cantact)
	#define USBD_PRODUCT_STRING_FS	 "cantact gs_usb"
	#define USBD_MANUFACTURER_STRING "cantact.io"
	#define DFU_INTERFACE_STRING_FS	 "cantact firmware upgrade interface"

	#define TIM2_CLOCK_SPEED		 48000000

	#define CAN_INTERFACE			 CAN
	#define CAN_CLOCK_SPEED			 48000000
	#define NUM_CAN_CHANNEL			 1

	#define LEDRX_GPIO_Port			 GPIOB
	#define LEDRX_Pin				 GPIO_PIN_0 /* green */
	#define LEDRX_Mode				 GPIO_MODE_OUTPUT_PP
	#define LEDRX_Active_High		 1

	#define LEDTX_GPIO_Port			 GPIOB
	#define LEDTX_Pin				 GPIO_PIN_1 /* red */
	#define LEDTX_Mode				 GPIO_MODE_OUTPUT_PP
	#define LEDTX_Active_High		 1

#elif defined(BOARD_usb2can)
	#define USBD_PRODUCT_STRING_FS	 "USB2CAN RCA gs_usb"
	#define USBD_MANUFACTURER_STRING "Roboter Club Aachen"
	#define DFU_INTERFACE_STRING_FS	 "usb2can firmware upgrade interface"

	#define TIM2_CLOCK_SPEED		 48000000

	#define CAN_INTERFACE			 CAN
	#define CAN_CLOCK_SPEED			 48000000
	#define NUM_CAN_CHANNEL			 1

	#define LEDTX_GPIO_Port			 GPIOA
	#define LEDTX_Pin				 GPIO_PIN_1 /* blue */
	#define LEDTX_Mode				 GPIO_MODE_OUTPUT_OD
	#define LEDTX_Active_High		 0

	#define LEDRX_GPIO_Port			 GPIOB
	#define LEDRX_Pin				 GPIO_PIN_3 /* green */
	#define LEDRX_Mode				 GPIO_MODE_OUTPUT_OD
	#define LEDRX_Active_High		 0

/*************** STM32F072 ***************/
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

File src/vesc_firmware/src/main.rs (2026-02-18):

#![feature(unsafe_cell_access)]
#![feature(never_type)]
#![no_std]
#![no_main]

use core::convert::TryInto;
use core::ptr;
use core::{cell::UnsafeCell, mem::MaybeUninit};

use canadensis_data_types::uavcan::node::health_1_0::Health;
use canadensis_data_types::uavcan::node::mode_1_0::Mode;
use canadensis_data_types::reg::udral::service::actuator;

use canadensis::{
    core::time::Clock,
    node::{
        self,
        data_types::{GetInfoResponse, Version},
        BasicNode, CoreNode,
    },
    requester::TransferIdFixedMap,
    Node,
};
use canadensis_bxcan::BxCanDriver;
use canadensis_can::{CanNodeId, CanReceiver, CanTransmitter, CanTransport};
use cortex_m::{interrupt::Mutex, iprintln};
use cortex_m_rt::entry;
use embedded_alloc::LlffHeap as Heap;
use fixed::types::I16F16;
use foc::{
    park_clarke::{inverse_park, RotatingReferenceFrame},
    pwm::{Modulation, SpaceVector},
};
use panic_semihosting as _;

use stm32f4xx_hal::{
    adc::{
        config::{AdcConfig, Resolution},
        Adc,
    },
    gpio::{AnyPin, GpioExt, Input, PinState, Speed},
    interrupt,
    pac::{SPI3, TIM1},
    prelude::*,
    rcc::*,
    signature::Uid,
};

extern crate alloc;
pub mod bsp;
pub mod comms;
pub mod config;
pub mod state;
pub mod utils;

use crate::{
    bsp::{clock::STM32F4xxCyphalClock, drv8301::DRV8301, six_pwm::STM32F4xxSixPwmDriver},
    comms::{
        CommSystem, CYPHAL_CONCURRENT_TRANSFERS, CYPHAL_NUM_SERVICES, CYPHAL_NUM_TOPICS, NODE_ID,
        PORT_CTRL_DUTY,
    },
    state::ControlMode,
    utils::{cos, sin},
};

static G_HALLS: Mutex<UnsafeCell<MaybeUninit<(AnyPin<Input>, AnyPin<Input>, AnyPin<Input>)>>> =
    Mutex::new(UnsafeCell::new(MaybeUninit::uninit()));
static G_PWMS: Mutex<UnsafeCell<MaybeUninit<STM32F4xxSixPwmDriver>>> =
    Mutex::new(UnsafeCell::new(MaybeUninit::uninit()));
static G_CONTROL: Mutex<UnsafeCell<ControlMode>> =
    Mutex::new(UnsafeCell::new(ControlMode::Disabled));

// Global allocator -- required by canadensis.
#[global_allocator]
static G_HEAP: Heap = Heap::empty();

fn initialise_allocator() {
    use core::mem::MaybeUninit;
    const HEAP_SIZE: usize = 16000;
    static mut HEAP_MEM: [MaybeUninit<u8>; HEAP_SIZE] = [MaybeUninit::uninit(); HEAP_SIZE];
    unsafe { G_HEAP.init(&raw mut HEAP_MEM as usize, HEAP_SIZE) }
}

///////////
// Main. //
///////////
#[entry]
fn main() -> ! {
    initialise_allocator();

    // Embedded boilerplate...
    let mut cp = cortex_m::Peripherals::take().unwrap();
    let dp = stm32f4xx_hal::pac::Peripherals::take().unwrap();

    let mut rcc = dp.RCC.freeze(
        Config::hse(24.MHz())
            .sysclk(168.MHz())
            .hclk(168.MHz())
            .pclk1(42.MHz())
            .pclk2(84.MHz()),
    );

    dp.DBGMCU.apb2_fz().modify(|_, w| {
        w.dbg_tim1_stop().set_bit() // Stops counting AND disables outputs!
    });

    let gpioa = dp.GPIOA.split(&mut rcc);
    let gpiob = dp.GPIOB.split(&mut rcc);
    let gpioc = dp.GPIOC.split(&mut rcc);

    let mut led_green = gpiob.pb0.into_push_pull_output();
    let mut led_red = gpiob.pb1.into_push_pull_output();
    led_red.set_high();
    
    unsafe {
        cp.DCB.enable_trace();
        cp.DWT.enable_cycle_counter();
        dp.DBGMCU
            .cr()
            .modify(|_, w| w.trace_ioen().set_bit().trace_mode().bits(0b00));
        cp.ITM.lar.write(0xC5ACCE55); // Unlock ITM registers
        cp.ITM.tcr.write(0x00010005); // AdvTBus ID = 1, Global ITM enable
        cp.ITM.ter[0].write(0b111); // Enables STIM1 & STIM0
        cp.ITM.tpr.write(0b1); // Enables STIM[7:0]
    }

    let drv = DRV8301::<SPI3>::setup(
        gpiob.pb5.into_push_pull_output_in_state(PinState::Low),
        gpiob.pb7.into_floating_input(),
        gpioc.pc9.into_push_pull_output_in_state(PinState::High),
        gpioc.pc10.into_alternate().speed(Speed::VeryHigh),
        gpioc.pc11.into_alternate().speed(Speed::VeryHigh),
        gpioc.pc12.into_alternate().speed(Speed::VeryHigh),
        dp.SPI3,
        &mut rcc,
    );

    let pwm_driver = STM32F4xxSixPwmDriver::setup(
        &mut rcc, dp.TIM1, gpioa.pa8, gpiob.pb13, gpioa.pa9, gpiob.pb14, gpioa.pa10, gpiob.pb15,
    );

    // Has external 2k2 pullups
    let hall1 = gpioc.pc6.into_pull_up_input();
    let hall2 = gpioc.pc7.into_pull_up_input();
    let hall3 = gpioc.pc8.into_pull_up_input();

    // Set up hall-sensor interfacing timer (TIM5)
    //
    // Mode of operation described in RM0390 16.3.18
    // OR refer to RM0440 28.3.29

    // Set up ADC's for voltage and motor current sensing
    // Multi-ADC Simultaneous injected mode?? Need to look into this later...
    // FIXME
    Adc::new(
        dp.ADC1,
        true,
        AdcConfig::default()
            .clock(stm32f4xx_hal::adc::config::Clock::Pclk2_div_4) // 21MHz
            .resolution(Resolution::Twelve),
        &mut rcc,
    );

    //dp.ADC_COMMON.ccr().write(|w| w.);

    // .external_trigger(adc::config::TriggerMode::RisingEdge, adc::config::ExternalTrigger::Tim_5_cc_1),
    //Adc::new(dp.ADC1, true, config, rcc);

    {
        let idx = (usize::from(hall1.is_high()) << 2)
            + (usize::from(hall2.is_high()) << 1)
            + usize::from(hall3.is_high());

        let angle = I16F16::FRAC_PI_3 * K_HALL_TABLE[idx];
        /*iprintln!(&mut cp.ITM.stim[0], "[INFO] HALL ANGLE: {}", angle);*/
        /*if idx == 0 || idx == 7 {
            iprintln!(
                &mut cp.ITM.stim[0],
                "[ERR] Invalid hall state {}... is the encoder plugged in?",
                idx
            );
        }*/
    }

    cortex_m::interrupt::free(|cs| unsafe {
        G_PWMS.borrow(cs).as_mut_unchecked().write(pwm_driver);
        G_HALLS
            .borrow(cs)
            .as_mut_unchecked()
            .write((hall1.into(), hall2.into(), hall3.into()));
    });

    unsafe {
        cortex_m::peripheral::NVIC::unmask(interrupt::TIM1_UP_TIM10);
    }

    ///////////////////////////////////////////////////////////////////////////
    //                           CANADENSIS SETUP                            //
    ///////////////////////////////////////////////////////////////////////////

    let pcan = dp.CAN1.can((gpiob.pb9, gpiob.pb8), &mut rcc);
    let can = bxcan::Can::builder(pcan)
        // APB1: 42MHz, BTR: 1Mbps, Sample: 70%
        // BS1: 14, BS2: 6, BRP: 2 (21MHz), SJW: 2 ig...?
        .set_bit_timing(0x015D_0001)
        .enable();

    let clock = STM32F4xxCyphalClock::new(dp.TIM5, &mut rcc);
    let id: CanNodeId = NODE_ID.try_into().unwrap();
    let mut uuid: [u8; 16] = [0x00; 16];
    unsafe {
        ptr::copy_nonoverlapping(Uid::get() as *const Uid as *const u8, uuid.as_mut_ptr(), 12);
    }
    let driver = BxCanDriver::new(can);
    let transmitter = CanTransmitter::new(canadensis_can::Mtu::Can8);
    let receiver = CanReceiver::new(id);
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

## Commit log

2024-09-04 Drivebase rover urdf v1 (#22)
    * Added initial robot xml files
    * [Description] Comment ROS2Control xacro includes, remove castor wheel, create a JointStatePublisher and add pkg info
    * Included joint-state-publisher in Dockerfile, Robot now renders in rviz2, Removed config file from CMakeLists
    * [Drivebase] Adds URDF for rover, sanitize xacro input
    * [Devcontainer] Update to jazzy
    * [Drivebase] Fix azipod azimuth axis, add joint limits for diff bar pivot
    * [Drivebase] Add steering joint limits
    * Added collision to wheels, inertia to frame parts
    * Added new broken file by mistake :skull:
    * added arbitrary inertia to wheel fork to stop gazebo complaints
    * Preliminar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
    [db_helpers.xacro, diff_drive_controller.yaml, inertial_macros.xacro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]
2025-02-05 Swerve controller (#31)
    * Add header file with a few of the declarations
    * Partially complete CMakelists.txt (add dependencies/building). Add instructions for building the package/static analysis
    * Add plugin.xml, add controller params file, continue progress on on_configure()
    * Swap to using complex numbers for kinematics
    * [Management] Update .gitignore to ignore .cache and compile_commands.json (clangd)
    * Beg 😼 for command 🫵 and state 👀 interfaces, rename kinematics -> modules in params, attempt to set commands
    * 🚀 complete skeleton 🦴 of controller, write and pass basic load controller test 🛂
    * [Style] Reformat with ament_uncrustify
    * [Description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
    [ros2_control.xacro, swerve_drive_controller.yaml, swerve_drive_controller_parameters.yaml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]
2025-03-14 Refactor urdf (#32)
    * Update rover pkg README to include setup instructions
    * Refactor rover URDF description files
    * QoL changes to Gazebo simulation launch file
    * Reformat rover w/ python-black
    * Remove black as a test_dep
    * Complete partial refactor, refactor gz_swervedrive.launch.py to fix time bridge
    * Cleanup, rename gz_swervedrive to rover launch for clarity
    [chassis.xacro, drivebase.xacro, gazebo_plugins.xacro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]
2025-03-21 Real sense camera setup (#37)
    * Testing camera real-sense
    * [UI] Realsense works in devcontainer on x64 host
    ---------
2025-03-22 Devcontainer compose (#38)
    * [Devcontainer] Switch to docker compose, needs testing with docker
    * [Devcontainer] Update gitignore
    * Fix jetson devcontainer setup
    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
2025-03-24 Bg431esc1 actuator (#36)
    * Set up Project. Set up header file and associated infrastructure.
    * Add functionality to read and categorize based on can id
    * Unify all controllers into one vector. Skill issue with C++ structs.
    * Create CAN mux class to allow multiple devices on the same bus
    * Implement the actual actuator
    * Revert random swerve drive changes
    * Fix xacro file
    * Fix xacro file
    * It is no longer unemployed.
    xian zia ta bu shi wu yong de ren
    * [bg431esc1_actuator] Testing node added
    * Add support for mechanism ratios and zeroing
    * Fix `from_bytes` to remove UB (I think)
    * Have the CAN worker check for a termination request
    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
    [bg431_motor.xacro, robot.urdf.xacro, ros2_control.xacro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]
2025-03-27 Add in depth explanation on how to configure new Jetsons (#41)
2025-07-05 Stepper Board (#59)
    * Write basic documentation for the stepper board
    * Write extremely basic power board specifications
    * Shift specifications to the correct locations
    * Update power system requirements
    * Correct typo in stepper driver spec and remove incorrect CPH spec
    * Create basic power supply section of the stepper driver
    * Correct capacitor selection and net labelling
    * Create most of the top level schematic
    * Assign power net classes and write basic power hub spec
    * Sketch channel schematic
    * Remove unnecessary capacitor
    * Attach h-bridge directoy to tmc5160, add missing capacitors, fix hybrid cap symbols
    * Tie 12VOUT and VSA to 12V supply instead of gate voltage reg circ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
    [channel.kicad_sch, power.kicad_sch, stepper-driver.kicad_sch]
2025-09-06 Can converter iteration 0 (#72)
    * Import elec common library
    * Redesigned linux automation can converter for out componenets
    * Replace regulator and tranceiver
    * Add jst pa connector, replace tranciever, replace componenets, remove unneeded files
    * Remove lockfile, remove old debug header, route new debug header
    * Finish layout and routing
    * Fix silkscreen
    * Create second version from scratch with rearranged components
    * Copy shinji over properly
    * Put back usb C file oops
    * Monkey
    * Rebase usb-can branch onto main
    * Add 100R series on crystal oscillator
    * Aaa
    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
    [Can_converter_v1.kicad_pcb, Can_converter_v1.kicad_sch, Can_converter_v2.kicad_pcb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]
2025-09-06 SWD Adapter V0 (#74)
    * vvv
    * Rebase swd-adapter onto main
    * Add README.md for SWD adapter
    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
    [can_terminator.kicad_pcb, can_terminator.kicad_sch, swd_adapter.kicad_pcb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]
2025-09-06 Stepper Controller V0
    [stepper-driver.kicad_sch]
2025-09-07 Cleanup can conv (#77)
    * Remove v1 can converter (Candlelight), canonicalize v2, update readme
    * Move can_conv_v2 -> can_conv
    * Add basic documentation
    * Remove files that were previously tracked unintentionally
    * Oops, Move can_conv -> can_conv_elec, ditto for can_term, swd_adapter
    * Fix symbol and footprint tables
    * Remove generated netlist
    * Move monke out of bluesat footprints, add more metadata to bluesat syms
    * Add TypeC connector to bluesat syms/fp
    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
    [Can_converter_v1.kicad_pcb, Can_converter_v1.kicad_sch, MCU.kicad_sch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]
2025-09-22 Add footprint for PQFN 5x6mm type E package (IRFH7440PbF MOSFET) (#79)
    * Add footprint for PQFN 5x6mm type E package (IRFH7440PbF MOSFET)
    * Add datasheet + description
    * Add correct paste layout
2025-09-22 Pqfn 6x5 footprint (#82)
    * rebase
    * Emergency patch - move courtyard to right layer
    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
2025-09-29 [CLEAN] Remove bg431esc1_actuator ROS package, mark can_converter_firmware as not to be built by colcon (#84)
    [urdf.xacro]
2025-10-01 USB Camera Setup etc.. (#83)
    * camera
    * Fixed up urdf for current rover design and added 3 depth cameras **Gazebo camera is a work in progress
    * Remove realsense, preinstall lichtblick in container
    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
    [chassis.xacro, db_helpers.xacro, depth_cams.xacro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]
2025-10-06 Fix all footprints (reduce solder bridges) (#88)
2025-10-07 More footprints for fine pitch parts (#89)
2025-10-11 Encoder Board
    [bluesat_encoder_board.kicad_pcb, bluesat_encoder_board.kicad_sch]
2025-10-13 Kinect Power Adaptor (#93)
    [kinect_adaptor.kicad_pcb, kinect_adaptor.kicad_sch]
2025-10-15 Review and fix encoder board (#94)
    [bluesat_encoder_board.kicad_pcb]
2025-10-18 Fix kinect adaptor board edge violation
    [kinect_adaptor.kicad_pcb]
2025-10-21 [ELEC] VESC REV.1 Complete (#95)
    * Add files for Cheap FOC-er. The Horrors.
    * remove IMU and servo from schematic
    * Change SWD header to meet spec and add XT30 connector (schematic)
    * Changed voltage divider resistor values
    * Removed unused 10 pin MCU header
    * Updated op amp resistors
    * Replaced CAN transciever with TCAN1462V
    * Changed screw holes from M3 to M2.5 (3.0 mm hole size)
    * removed unused connectors
    * removed signal and power ground connection
    * removed 3V3 regulator for MOSFET driver, changed VSENSE voltage divider and flags to match
    * added charge pump for CAN transciever 5V supply
    * replaced VSENSE resistor with std values in series
    * replaced 330u electrolytic caps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
    [CAN.kicad_sch, IMU.kicad_sch, Power.kicad_sch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]
2025-10-21 [ELEC] Usb power board REV.1 (#92)
    * [ELEC] Start work on USB Hub
    cant remember need this on desktop
    add footprints and symbols for USB hub
    spam capacitors
    Add footprints, Create 5gb hub schematic
    Setup 20gbps hub, add usb C
    Add VCORE power modules
    blah bla blah
    spamming discord need this on my desktop
    Fixed power lines and added 3v3 and 1v17
    Add OCP for 5V USB ports and each kinect
    Forgot
    add connectors
    Setup STM busses to HUB chips for flasing memory
    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
    [STM_memory.kicad_sch, connectors.kicad_sch, powerboard.kicad_sch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]
2025-10-21 [ELEC] Main power board REV.1 (#96)
    * Make KiCad proj, import elec common lib
    * Calculate maximum switching time for power MOSFET
    * Driver circuit sim done
    * Make preliminary G4 schematic
    * Copy over power stuff from stepper
    * Wire channels on schematic
    * Add crystal, swdio header, other misc board stuff to MPM
    * Finish schematic besides bypass capacitors
    * Fix bypass cap grounding, add estop on charge pump, fix pin naming on MCU.
    * Update pinout on cubemx
    * Make the bus real
    * Add caps for other components
    * Do switch on time calculation
    * Schematic done (?)
    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
    [gate_driver.kicad_sch, main_power_hub.kicad_pcb, main_power_hub.kicad_sch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]
2025-10-21 [ELEC] Can converter board REV.2 (#97)
    * Remove whimsy, needs bluesat logo
    * idk what this is honestly
    * Rebase footprints and fix ALL DRC errors
    * added version number
    * remove mystery pull down resistor
    * hello??
    * Fix 3D model for usb port
    * Chamfpher
    * ashdakjsdhjkahfklsadfsfd
    * Give in to Evan tism (remove IDC connector and add 2xM2.5 mounting holes)
    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
    [MCU.kicad_sch, can_converter.kicad_pcb, can_converter.kicad_sch]
2025-10-21 [ELEC] Stepper board REV.2 (#98)
    * Resolve issues on the stepper board found in initial testing
    * Fixed singular character
    * Fix key`
    * 变身
    * Remove .net file
    * Remove unrelated file from branch
    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
    [channel.kicad_sch, power.kicad_sch, stepper-driver.kicad_sch]
2025-10-21 [ELEC] Computing power board REV.1 (#99)
    * https://www.youtube.com/watch?v=6n3pFFPSlW4
    I love ice coffee
    stm32 is
    a scary platform
    * Complete first draft of compute power schematic
    * Is sisyphus happy?
    * uwu
    * Add big 19V regulator
    * fn
    * Baa
    * Can converter iteration 0 (#72)
    * Copy shinji o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
    [buck-12v.xls, buck-19v.xls, buck-5v.xls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]
2025-10-21 [ELEC] SWD Adaptor board REV.2 (#100)
    * The IDC 14 pin to 6 pin converter
    * Final touches
    * Fix IDC6 pinout :sob:, reroute
    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
    [swd_adapter.kicad_pcb, swd_adapter.kicad_sch]
2025-10-22 [ELEC] REV markers on all PCB's, Fix USB hub passives (#101)
    Add mounting holes to all PCB schematics
    [STM_memory.kicad_sch, VH4_extender.kicad_pcb, VH4_extender.kicad_sch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]
2025-10-25 [ELEC] Fix usb hub (#104)
    * hopefully evan hasn't landed yet
    * DRC pass
    * Fatter power
    * GG Sean
    * these mosfets are the death of me
    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
    [powerboard.kicad_sch]
2025-10-25 [ELEC] MPM connector fix (#105)
    * Fix MPM, use correct TVS symbol, change XT90 polarity
    * Use bluesat TSSOP8 footprint
    [main_power_hub.kicad_pcb, main_power_hub.kicad_sch, mosfets.kicad_sch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]
2025-10-26 USB HUB fix for the order(#106)
    * Same current loop fix just on a new branch this time
    * Move passives near connectors again
    * Mosfet-cap ground zone added
2025-10-26 [ELEC] Tie MP2459GJ EN pin to Vbus (#107)
    [power.kicad_sch]
2025-11-15 Fix MPM/CPM Medium NMOS symbol, DGS -> GSD
    [connectors.kicad_sch, gate_driver.kicad_sch]
2025-11-23 Remove unused pins on VESC schematic (#121)
    [CAN.kicad_sch, Power.kicad_sch, STM32F4 64LQFP.kicad_sch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]
2025-12-02 [VESC] Swap phase A and C MOSFET labels (#123)
    [Power.kicad_sch, mosfets.kicad_sch, vesc.kicad_pcb]
2025-12-02 Fix rotated IDC6 on CPM/MPM/VESC/Stepper/USB Hub (#120)
    * Fix rotated IDC6 on CPM/MPM/VESC/Stepper/USB Hub
    * Fix VESC
    [STM32F4 64LQFP.kicad_sch, STM_memory.kicad_sch, computing-power-hub.kicad_sch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]
2026-01-06 Add scaled versions of other footprints (vibes mech)
2026-01-16 Fix can trans (#126)
    * Fix STB on can trans for CPH
    * Fix MPM can trans
    * Fix StepDriv Can trans
    * Fix can trans on UPB
    [STM_memory.kicad_sch, computing-power-hub.kicad_sch, main_power_hub.kicad_pcb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]
2026-01-29 Add utils common to all devices to a shared library (#128)
    * Pull in embedded common utils from the bootloader branch
    * Remove SplitController and Led, move buffer outside of Controller
    * Fix formatting of comments explaining UART/WS2812 lookup table
    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
    [argb.rs, clock.rs]
2026-01-29 Fix AMBER colour in embedded_common (#129)
    [argb.rs]
2026-02-04 Fix M2.5 footprint
2026-02-05 Correctly pass the frame length out of the receive function
2026-02-07 Stepper drivebase firmware (#124)
    Credits:
    Firmware Pioneer - Jonah
    Cyphal Whisperer - Jonah
    I2C 2IC - Kai
    QSPI Wizard - Evan
    Professional Refactoring, Inc. - Jethro, Evan, Aavin
    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
2026-02-09 Invert steppers to be CCW +ve (#134)
    [drivebase.rs]
2026-02-14 Report health status and provide a remote reset for the drivebase (#136)
    * Report health status and provide a remote reset for the drivebase
    * Status codes based on TMC errors
    [drivebase.rs, main.rs, stepper_bus.rs]
2026-02-14 Glorp operator respect button ----> (Fix the SM0*B-PASS connectors type shit) (#142)
2026-02-18 Stepper FW Jonah's docs/style pass (#144)
    * Documentation and style pass
    * Add note about running in prod
    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
2026-02-18 Add VESC firmware in correct format: sowwy Jonah (#143)
    * Add VESC firmware in correct format: sowwy Jonah
    * Move scripts to embedded common
    * Update debug/run instructions
    [clock.rs, drv8301.rs, main.rs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]
2026-02-21 elec_common library cleanup (#146)
    Footprints:
    - Added extra common pads (9, 10) to the 6-in-1 USB TVS diodes (footprint UDFN8_3P3X1_517CB_QNS)
    - Can someone check the solder paste layer is sensible?
    - Created improved PowerPAD footprint for the TPS61175
    Symbols:
    - Deleted unused and unstocked TPS565201 symbol
    - Fixed incorrect package for the QSPI flash (SOP-8 -> Winbond 3x2, 0.50)
    - Changed ASM330 to ISM330; added pin RES to symbol to avoid leaving pins floating that the datasheet recommends be tied high or low
    - Just tie to GND
    - Added ARCh legality warning to magnetometer (LIS2MDL)
    - Added IDC_6P header symbol coupled with known good IDC6 footprint
    - Added datasheets and improved name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
2026-02-23 Update WS2812-2020 footprint, add WS2812B-5050 footprint (#156)
2026-02-28 Cleanup .gitignore (#159)
    * Cleanup .gitignore
    * Amend gitignore
    * Additional KiCAD files
    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
2026-02-28 [ELEC] CPM v2.0 (#148)
    * Add changelog and small changes
    * aaa
    * I remember
    * Fucking
    * Silky
    * Delete src/computing_power_hub_elec/CHANGELOG.md
    * Clean up (fix footprints, DRC etc.) for production
    * Change 0.3/0.4 mm vias to 0.3/0.45 for JLC
    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
    [computing-power-hub.kicad_sch, connectors.kicad_sch, regulators.kicad_sch]
2026-02-28 [ELEC] Stepper board v3.0 (#147)
    * Significantly reduce the number of components based on testing data
    * Before...
    * fff
    * Layout
    * Silkscreen
    * にゃー
    * Clean up for production (purely cosmetic fixes save for shifting some vias slightly to the left for clearance)
    * Fix JLC via complaint by changing all 0.3/0.4 mm vias to 0.3/0.45
    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
    [channel.kicad_sch, power.kicad_sch, stepper-driver.kicad_sch]
2026-02-28 [ELEC] Encoder connector board v1.0 (#150)
    * Add safiy's files
    * Changes to footprint library
    * update pcb routing
    * routing + change buck IC
    * Small changes
    * change schematic to be correct with new power stage
    * Encoder connector board
    * Comply with versioning scheme, add silkscreen art
    * oopsie silkscreen overlap
    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
    [connector_board.kicad_pcb, connector_board.kicad_sch]
2026-02-28 [ELEC] Neo adaptor v1.0 (#149)
    * Stupid fvcking NEO adaptor
    * Not any less stupid, add some silkscreen art
    * MIXED UP RADIUS AND DIAMETER OOPSIE
    * Sean has been collared
    [neo_adaptor_elec.kicad_pcb, neo_adaptor_elec.kicad_sch]
2026-02-28 [ELEC] Main power board v2.0 (#151)
    * Fixed MPM schematic as per errata from 4th Feb 2026
    * Layout done, 64x64mm board w/ changes
    * Almost done routing
    * add shottky to drain
    * MPM almost finished small routing on desktop needed
    * Finished routing
    * Perfect DRC and silkscreen removed from bottom
    * Add silkscreen art and versioning
    * WWW
    * Perfect footprint pass and DRC pass, successful rebase and fix, ready to order, SEAN
    * Add channel indicator silkscreen
    * Remove log files
    ---------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
    [gate_driver.kicad_sch, main_power_hub.kicad_pcb, main_power_hub.kicad_sch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]
2026-02-28 [ELEC] System power board v1.0 (#152)
    * Added system power hub kicad project stuff
    * Added libs for SPM
    * [WIP] Copied KiCAD proj from MPM, modified schematic for SPM
    * Removed unnecessary ioc file
    * Draft SPM PCB layout
    * Fixed XT connector routing, rewired power stuff (attempted to), made board smaller, more routing/layout progress
    * Draft layout done, need to continue routing and decide on GPIO
    * Routed everything except GPIO
    * More basic routing updates
    * Mosfet DGS -> GSD, CAN tranceiver STB -> GND
    * Completed channel wiring/routing, vbus sense routed
    * Small routing changes
    * Fix SPM schematic as per errata 04-02-2026
    * Finished PCB layout & routing for errata
    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
    [gate_driver.kicad_sch, mosfets.kicad_sch, power.kicad_sch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]
2026-02-28 [ELEC] BESC (#153)
    * Setup Vesc2 files
    * Elec boilerplate
    * recreate gate driver looking less ugly
    * Configured STM32 IOC file for outputs
    * configure STM32G4 and route
    * Finish schem bar mosfet footprints
    * made evans changes
    * Final commit before routing just incase
    * Most the layout done im playing cs2
    * finished routing :)
    * Fix small global label error
    * HELLO FROM ARCH LINUX (minor changes for QOL when soldering)
    * Update footprints of connectors and reroute
    * Changes to power zones and mosfet inputs
    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
    [gatedriver.kicad_sch, mosfets.kicad_sch, vesc2.kicad_pcb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]
2026-02-28 [ELEC] Led beacon (#154)
    * Setup led_beacon file for someone to work on it eyes emoji
    * Add readme and board dimentions in the PCB
    * LED Beacon finished
    * Move LED beacon to correct folder
    * Fix bypass caps lmao
    * Comply with versioning scheme
    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
    [led_beacon.kicad_pcb, led_beacon.kicad_sch]
2026-02-28 Refactor ros (#161)
    * Begin refactor
    * More progress
    * Moar progress
    * Fix init.bash to be runnable from anywhere
    * Fix swerve_drive_controller compilation
    * Update swerve drive controller, no more warnings 😸
    * Fix simulation, format files
    * Clean up ros2control usage in URDF
    * Fix control_station readme
    * Scuffed angle optimization code, limit to ±90 deg
    * Make mock cyphal VESC driver to test integration, pipe it up in rover pkg
    * Mmm less toasty
    * Add `uv` python package manager to devcontainer
    [bg431_motor.xacro, core.xacro, cyphal_vesc_driver_plugin.xml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]
2026-02-28 Add basic CI pipeline for elec (#165)
    * Add basic CI pipeline for elec
    * Fix trigger
    * Switch to cached image
    * Fix path
    * Fix path
    * Nicer printing
    * Install kicad
    * Try skip 3d libraries
    * Check exit properly
    * Check exit properly
    * Going to kms
2026-03-12 Additional tmc registers (#172)
    * Add support for arithmetic operations TMC unit types
    * Add a direct variant of the XTarget register to allow for Solenoids and
    DC motors
    * Format file
2026-03-24 [BREAKING] stepper_drivebase_firmware update for HW:r3p0 (#173)
    * Bump firmware and hardware version
    * Invert drivebase r3p0 stepper_drivebase_firmware
    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
    [drivebase.rs]
2026-03-24 Shovel stepper (#174)
    * Implement basic linac control
    * Actually commit current limits (I think)
    * Readd channel inversion logic
    * Re-add unique colour pattern
    * Tested on rover, flip some knobs
    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
    [main.rs, motion.rs]
2026-03-27 Report the current stepper angle from the TMCs (#175)
    * Report the current stepper angle from the TMCs
    * Start publishing the position messages
2026-03-27 Obc utils (#176)
    * caninit.sh set txqueuelen=1000
    * Minorly update wasd and run_steering script, remove tankcontrol.sh, change wasd speeds, add kinect to Udev rules
    * [OBC] arm script
    * Update OBC utils for comp
    * Ignore mediamtx
    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
2026-03-27 Obc utils moar (#179)
    * BESC bringup -- LEDs and CAN seem to work, commutation untested
    * Working commutation
    * Add encoders back into the mix
    * Add SVD file loading to GDB init script
    * BESC CAN downgrade from FD to classic for comp drivebase compatibility
    * Initial commit of deckard
    * Actually update wheel orientation
    * Patch in CANFD support on Linux
    * Try to add VESCs and fail sadly
    * Fix really stupid mistakes
    * Consolidate motor commands into sets of 4
    * More unmaintainable bs
    * idk
    * Attempt to fix wheel drive directions
    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
    [main.rs]
2026-03-27 Deckard (#180)
    * Skip steering wheels if they're already in position
    * Halt VESCs before steer motions
    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
2026-03-27 Get new camera scheme working on rover, sorry for merging early aavin (#182)
2026-04-26 Rename links to remove -502 midfix?? Change devcontainer workspace!! Remove unused KiCAD log files (#195)
